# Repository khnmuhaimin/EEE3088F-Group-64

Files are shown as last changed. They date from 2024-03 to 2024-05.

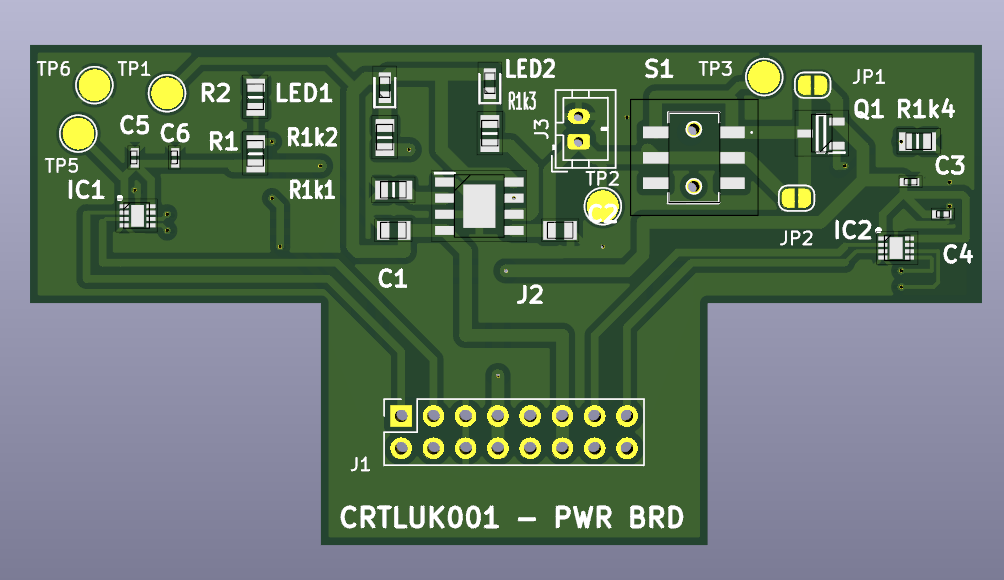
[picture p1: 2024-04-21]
power/Project Files V3/ProjectFiles/FrontPCB.png

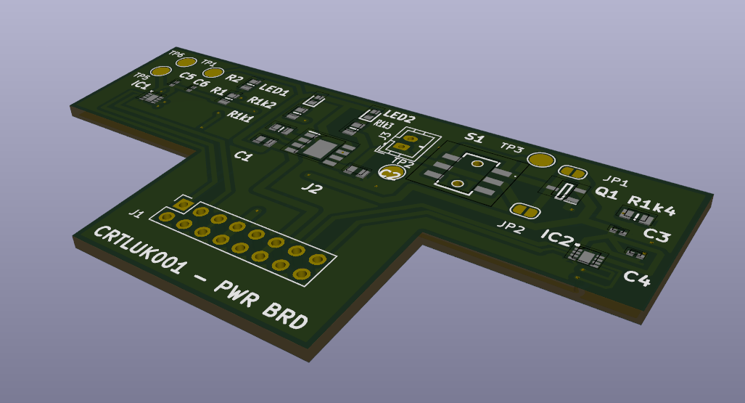
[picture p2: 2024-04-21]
power/Project Files V3/ProjectFiles/3DPCB.png

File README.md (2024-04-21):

# EEE3088F Micromouse Design Project

## Overview

This repository contains the design and implementation of the sensing and power subsystems for a micromouse project. The sensing subsystem is responsible for detecting walls and approximating distances to these walls using infrared (IR) sensors. The power subsystem is responsible for supplying power to the rest of the micromouse and controlling the motors used to move the micromouse around. This README provides an overview of the project.

## General Micromouse Features

- **Wall Detection**: Detects the presence of walls in three directions: forwards, left, and right.
- **PCB Design**: Includes the design of a custom PCB that integrates with the micromouse.
- **Autonomous Navigation**: Explores and solves a maze autonomously.

## Necessary Additional Components
- **STM32L476 microcontroller**
- **Motherboard PCB with PIN connections**
- **Wheels and motors for movement (multi-rotational drawing approximately 200mA each**
- **Battery LiPo 800mAh 3.7V**
- **Battery, Power and Sensing headers need to be purchased and soldered on during assembly**
- **5V Power supply for charging**
- **Device capable of running MATLAB**

## Installation

1. Clone the repository:

    ```
    git clone https://github.com/khnmuhaimin/EEE3088F-Group-64.git
    ```

2. Navigate to the project directory:

    ```
    cd EEE3088F-Group-64
    ```

3. Use KiCad to open up the project files for the custom PCB design.

## License

This project is licensed under the MIT License. See the `LICENSE` file for details.

## Contributors (Group 64)

- Luke Carter(CRTLUK001)
- Muhaimin Khan(KHNMUH063)

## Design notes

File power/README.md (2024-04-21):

# Power section 
Relevant files related to the power section relating to the PCB files, schematics and images from the finished product

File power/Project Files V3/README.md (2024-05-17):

# Project Files
Power project files v3 which are the final files for the project

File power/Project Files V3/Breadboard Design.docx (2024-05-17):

Breadboard Design:

Basic requirements:

- 1.5A output current
- 12V output voltage
- 2.4V transition on
- 0.5V transition off
- Current draw no more than 1mA on input stage
- Circuit operates at 12V
- Voltage across load is at least 11.5V at 1.5A
- Switching speed ON-OFF/OFF-ON less than 1us

Possible Transistors that reach the above requirements:

2N2222 – not enough current can go through

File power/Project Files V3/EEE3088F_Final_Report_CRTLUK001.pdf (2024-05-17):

# Final Design Report

Micro-mouse Power Subsystem


Prepared by:
Luke Carter

Prepared for:
EEE3088F
Department of Electrical Engineering University of Cape Town

May 17, 2024

# Declaration

1. I know that plagiarism is wrong. Plagiarism is to use another’s work and pretend that it is one’s own.
2. I have used the IEEE convention for citation and referencing. Each contribution to, and quotation in, this report from the work(s) of other people has been attributed, and has been cited and referenced.
3. This report is my own work.
4. I have not allowed, and will not allow, anyone to copy my work with the intention of passing it off as their own work or part thereof.

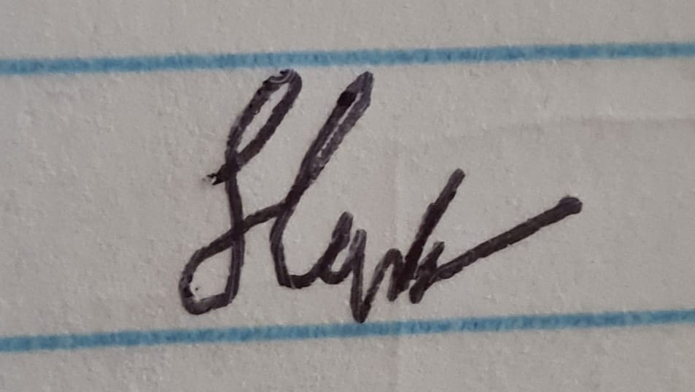
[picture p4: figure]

May 17, 2024

Name Surname | Date

ii

# Contents

1 Introduction | 1
2 Requirements Analysis | 2
3 Subsystem Design | 6
4 Acceptance Testing | 11
5 Conclusion | 18
Bibliography | 19

iii

# Chapter 1

# Introduction

### 1.1 Problem Description

This project aims at investigating and implementing a viable power system as a subsection to a micro-mouse system, capable of powering all necessary components of the system by utilizing a battery. The power subsection is part of a greater system under which two people are working towards creating a micro-mouse [1]. The micro-mouse is being created to complete a maze in the shortest time possible, where the mouse will first go through an entire maze recording the dimensions and paths of the maze, before calculating the fastest route through the maze and completing that journey, all within a 20-minute time limit, through the use of algorithms utilizing the physical components the students are designing. The other student will be working on the sensing subsystem, which will be used for the micro-mouse to detect walls for coordinated movement through the maze. Alongside these two subsystems, a processor and motherboard have been provided for integration purposes between the two subsystems allowing for control of the micro-mouse’s movement at a later stage of development.

This report focuses on the development of the power subsystem to ensure power is given to the other subsystems and to the motors, which will be needed for the movement of the micro-mouse, and to be able to communicate important information to and from the processor to allow for coordinated movement and battery charge control.

### 1.2 Scope and Limitations

This project has a specific focus on the power subsection of the micro-mouse, with the focus for this subsection establishing a working power system capable of charging batteries needed to power the system once it is unplugged from the 5V power storage and then using the charged batteries to power the micro-controller, motors and other parts of the board. Although the sensing subsection will ultimately utilize power from the power system, it is not within the scope to provide the other subsection with a specific power as they will receive the power straight from the micro-controller itself.

Limitations in the project include budget, dimensions of the PCB, specifications of parts provided to the students and components available at JLCPCB, which all need to be considered when designing the board. Full freedom outside of this is given to students with regard to choosing components and board shapes.

### 1.3 GitHub Link

https://github.com/khnmuhaimin/EEE3088F-Group-64.git

# Chapter 2

# Requirements Analysis

### 2.1 Requirements

The requirements for a micro-mouse power module are described in Table 2.1.

Table 2.1: Requirements of the power subsystem for the micro-mouse system.

Requirement ID | Description
R01 | Use a battery as the method of power for the subsystem
R02 | Operate two motors from available pins
R03 | Provide an analogue connection to verify the battery state of charge
R04 | Battery charged from the 5V pin
R05 | The system needs an on/off switch for the battery
R06 | The connector for the PCB needs to be in a tab off the board for a proper connection with the motherboard
R07 | Make PCB as small as possible to minimize the distance from the centre of rotation
R08 | Provide power to all subsections of the micro-mouse and components linked to the power sub-section e.g. the motors.

### 2.2 Specifications

The specifications, refined from the requirements in ??, for the micro-mouse power module are described in Table 2.2.

Table 2.2: Specifications of the power subsystem derived from the requirements in Table 2.1.

Specification ID | Description
SP01 | Battery is able to sustain a draw of 400mA at 4.2V
SP02 | Two Motors capable of rotating clockwise and anti-clockwise, each drawing 200mA,

2.3. Testing Procedures
SPO3 | 3.3 maximum output voltage for BATT_ADC line
SPO4 | Battery charged at 4.2V
SPO5 | Switch must handle 1A in on state and less than 1mA in off state
SPO6 | Tab height must be 18mm or greater and width height of no more than 35mm
SPO7 | PCB on micro-mouse must not exceed the distance from center of rotation of 100mm
SPO8 | Motors provided with 4.2V ±5%

### 2.3 Testing Procedures

A summary of the testing procedures detailed in chapter 4 is given in Table 2.6.

Table 2.5: Acceptance Testing Proecdures

Acceptance Test ID | Description
AT01 | Verify the battery is receiving 4.2V from the battery charger
AT02 | Verify the battery charger is getting 5V input
AT03 | Verify the switch is allowing 4.2V through when in On state
AT04 | Verify the switch is not allowing voltage through when in Off state
AT05 | Verify battery charger is outputting volt-age, used to verify there is not a short be-tween the battery connector and charger
AT06 | Verify the motor 1 will spin clockwise when switch is on, Pin 14 is high and Pin 16 is low

2.4. Traceability Analysis

Table 2.6: Acceptance Testing Proecdures

Acceptance Test ID | Description
AT07 | Verify the motor 1 will spin anti-clockwise when switch is on, Pin 16 is high and Pin 14 is low
AT08 | Verify the motor 2 will spin clockwise when switch is on, Pin 2 is high and Pin 4 is low
AT09 | Verify the motor 2 will spin anti-clockwise when switch is on, Pin 4 is high and Pin 2 is low
AT10 | Verify BATT_ADC is outputting voltage when switch is on
AT11 | Verify BATT pin which will be connected to the microprocessor is outputting a volt-age of 4.2V
AT12 | Check resistors and capacitors in the cir-cuit are not shorting

### 2.4 Traceability Analysis

The show how the requirements, specifications and testing procedures all link, Table 2.7 is provided.

Table 2.7: Requirements Traceability Matrix

# | Requirements | Specifications | Acceptance Test

1 | R01 | SP01 | AT01
2 | R02 | SP02 | AT06, AT07, AT08, AT09
3 | R03 | SP03 | AT10
4 | R04 | SP04 | AT01, AT03
5 | R05 | SP05 | AT04, AT05
8 | R08 | SP05 | AT11

R06, SP06, R07, SP07 are dimensions for the board that have been provided, no acceptance testing needs to be done for this, it just needs to be incorporated in the design section of the project AT12 are general tests that do not relate to the requirements or specifications of the project and are used to verify the board is operating correctly when it arrives

### 2.4.1 Traceability Analysis 1

R01 is the requirement that the system must be powered by a battery, with SP01 as the specification that it can sustain a draw of 400mA at 4.2V, which is verified using AT01 to check if the pins are

2.4. Traceability Analysis

producing that voltage

### 2.4.2 Traceability Analysis 2

R02 is the requirement that using available pins, two motors need to be operated, with SPO2 that they can rotate in multiple directions, each with a draw of 200mA. The motors will be spun based on a signal from the microcontroller, where there are 4 different signals, two for each motor, when one is high and another is low, it will spin in a certain direction. Using AT06, AT07, AT08 and AT09 we can verify for both batteries that they will spin in the correct direction based on the input from the microcontroller.

### 2.4.3 Traceability Analysis 3

R03 is the requirement that an analogue voltage connection is needed to verify the state of charge of the battery so the system can alert you if it is running low. SP03 indicates the max voltage on that line based on what the microcontroller can take, which will be tested using AT10 to test if the voltage is not exceeding that limit.

### 2.4.4 Traceability Analysis 4

R05 requires the battery to be charged from a 5V pin, with SP04 that the battery itself needs to be charged at 4.2V, meaning a battery charger is needed to supply 4.2V to the battery from the original 5V, which is tested using AT01 and AT03 to check correct voltages.

### 2.4.5 Traceability Analysis 5

R05 requires a working switch with SP05 that can handle 1A in on-state and 1mA in off-state. To verify the switch is working correctly AT04 and AT05 is used.

### 2.4.6 Traceability Analysis 6

R08 requires all subsystems are provided 4.2V with SP08 specifying the motors also be provided 4.2V, which is tested using AT11 which is connected to the system and motors.

# Chapter 3

# Subsystem Design

### 3.1 Design Decisions

### 3.1.1 Design Process

Within our system, different areas needed to be focused upon, each with its own challenges that needed to be solved. The three main areas of this design process were the battery charger, battery and switch system, and the motors. Within each area of the design process, several challenges need to be factored into how the final PCB was to be designed: the budget for this project was incredibly tight and certain components would therefore be out of our price range so that had to be accounted for:

- Budget - The budget for this project was incredibly tight, which made it harder when select parts as too many of certain parts would exceed the budget given, therefor considerations had to be made for each area to ensure that this project stayed below that range. The budget can be seen in the figure below:

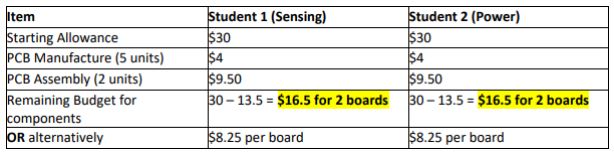
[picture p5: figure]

Figure 3.1: Budget
- Space - The PCB board had its own constraints, whereby a tab needed to be included in the design, and the dimensions of the board needed to take into consideration the turning circle of the micro-mouse such that the width and length of the PCB did not exceed the lengths. Measurements and calculations can be seen in the figure below:

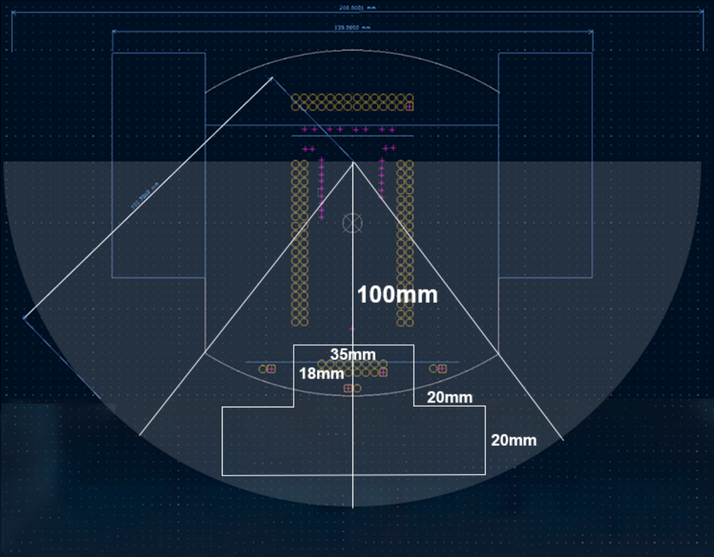
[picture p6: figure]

Figure 3.2: PCB Board Dimensions

3.1. Design Decisions
- Battery - Although the system has a good sized battery, considerations do need to be made to ensure that the components we use do not over-deplete the battery as this project needs to be able to last for over 20 minutes while navigating a maze, and using too much current will deplete the battery faster.

With the above factors in mind, each section of the sub-system can be designed accordingly to ensure that the issues mentioned above are less likely to arise.

Battery Charger

The battery charger is an integral part of the design as it will be used to charge the battery for the whole system utilizing a 5V input from the microprocessor. A voltage divider circuit could be used to reduce the voltage to the correct voltage but lacked circuit protection, and an IC charger made more sense to ensure correct protection was integrated. A primary concern with the IC battery charger was the budget aspect, as through the website the PCBs would be ordered through, JLCPCB, and certain parts would have extended costs based on whether the part was in regular production or not, resulting in the extra cost of 3 dollars for extended parts. It became apparent that the parts needed for the other sections would need to be extended, so a basic part for the charger would reduce budget concerns. This was the first major design decision, as choosing a battery charger with no extended cost greatly decreased the budget concerns, and the battery charger TP4056-42-ESOP8 became the best choice over the other options as it had no additional costs.

Switch and Battery system

Switches were a problematic area of the design as there was only one basic part switch which was a push button, which would require extra circuitry like MOSFETs, transistors, resistors and capacitors to get it to work correctly, which added complication with verifying if the circuit would work correctly, with the added specification that the switch must be added to handle 1A in the on state. This was the second major design decision made, to utilize an extended part for the switch to allow for a better selection of switches based on the type of switch and current it could handle. Based on these decisions, it was decided to use a switch called MS-22D28-G020 with verifiable data sheets and footprints for easy integration into the system, capable of handling 1A at 6V.

Motor system

The subsection required two systems each capable of running a motor at 200mA at 4.2V. Originally, the design decision was made to create an H-bridge configuration utilizing various parts such as MOSFETs and transistors to create a switching system to allow for the rotation of the motors in different directions, however, it became complicated to select the parts and to verify that the H-bridge design would function correctly with the complications of shoot-through being present in the designs. Integrated Circuits (IC) available on JLC included shoot-through protection making it a more preferable option compared to building a circuit from scratch. The third major design decision was deciding to use an H-bridge driver DRV8837DSGT, which although had an extended cost, had shoot-through protection and was designed to function according to our needs.

3.1. Design Decisions

### 3.1.2 Final Design

The following design integrates the decision decisions made above, utilizing the parts mentioned to create a system whereby a battery charger is used to charge the battery, the battery provides power to the circuit upon the switch being switched on, protected by a polarity protector. The battery will power two motors, the microprocessor and all things connected to that, and an ADC line in which the state of charge of the battery can be checked. Standard capacitors are used as a discharging method throughout, with resistors and LEDs for the TP4056 selected based on the datasheet for the component. The BATT_ADC line is protected by utilizing large resistors to protect the microprocessor.

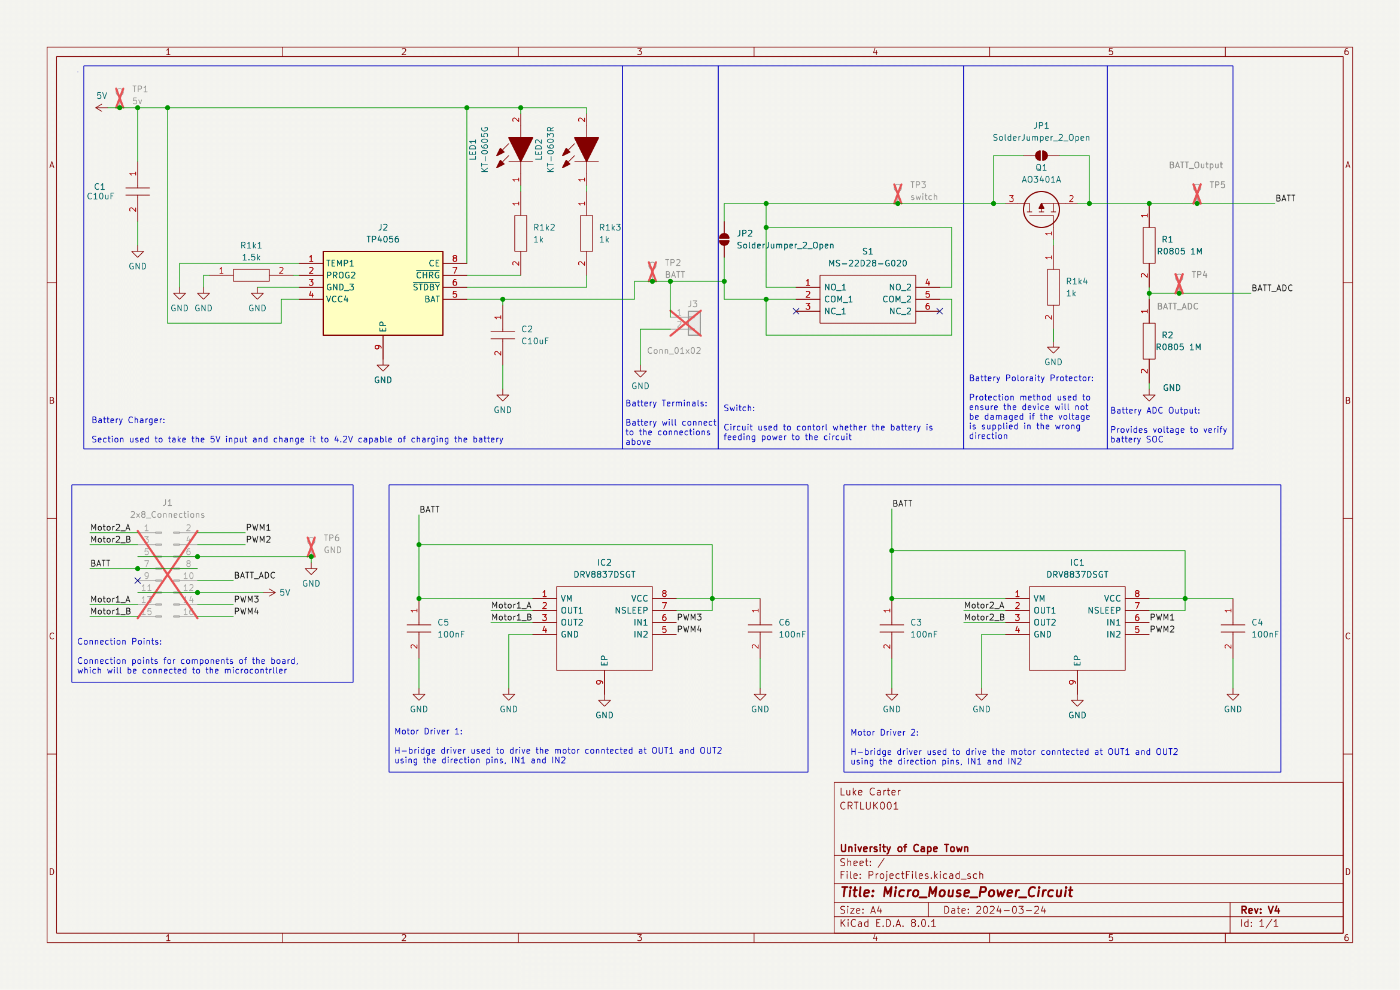
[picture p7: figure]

Figure 3.3: Schematic Drawing

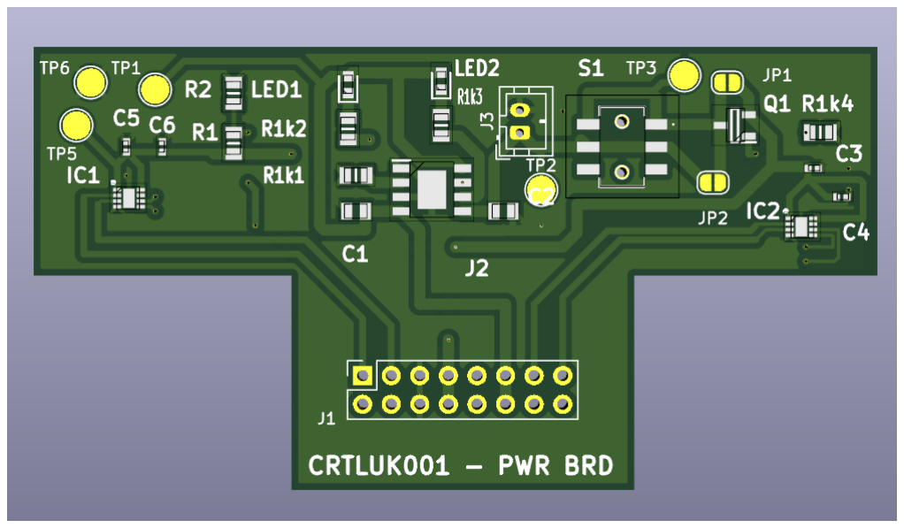
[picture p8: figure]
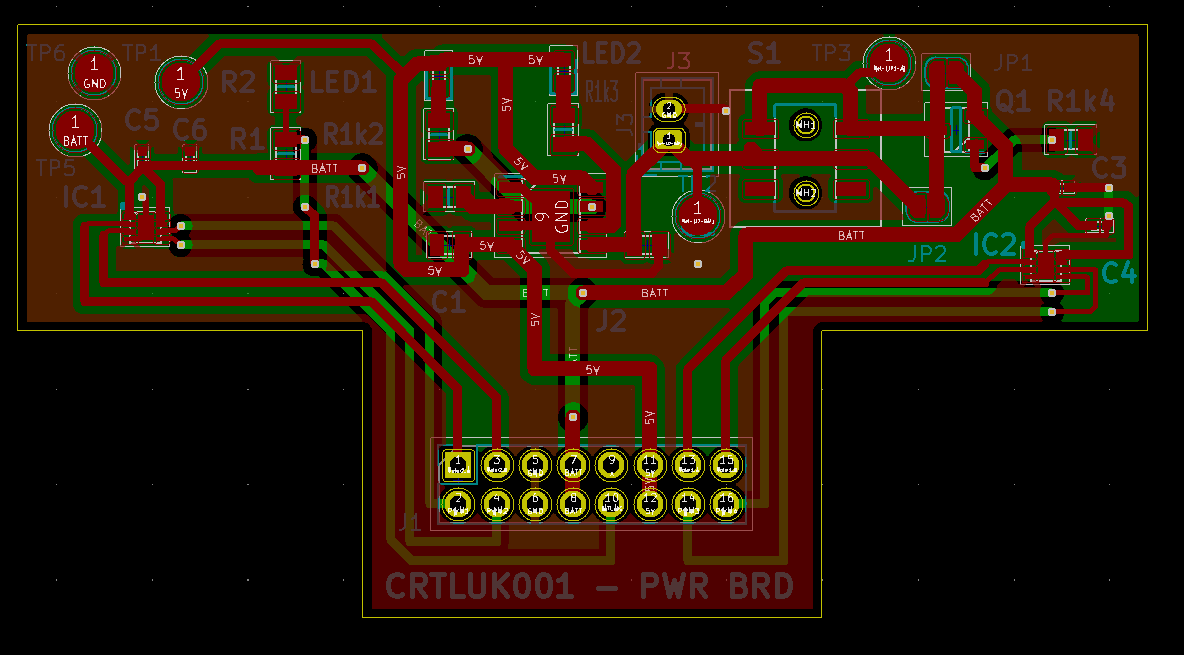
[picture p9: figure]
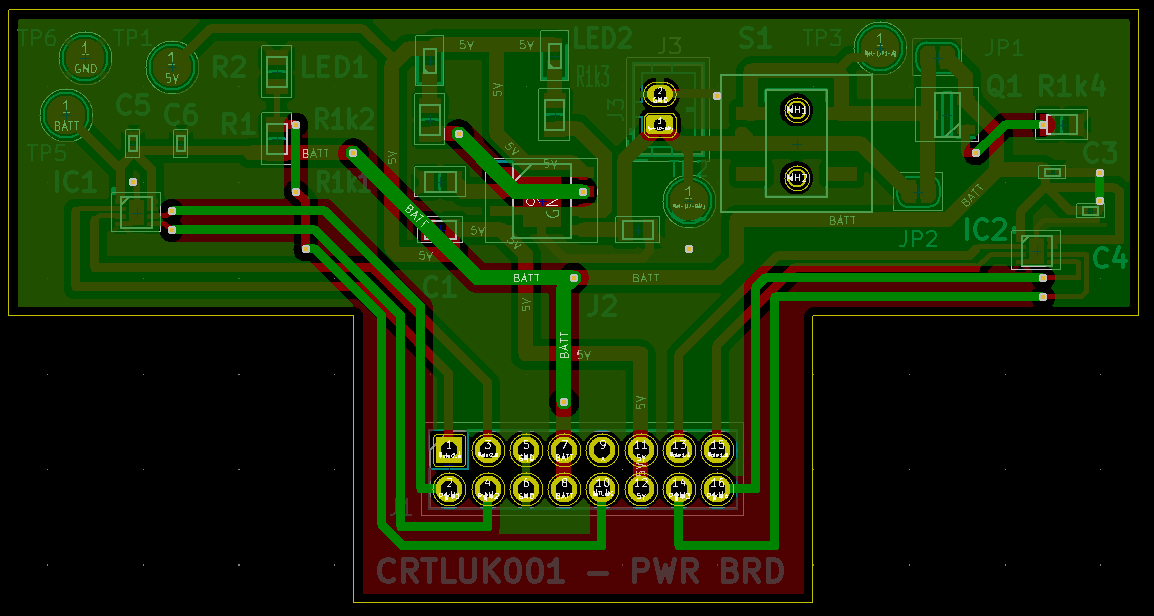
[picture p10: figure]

(a) Front PCB | (b) Back PCB | (c) 3D PCB

3.2. Failure Management

### 3.2 Failure Management

Table 3.1: Failure Management

Name | Description
Switch Bypass | The switch is an area of concern because if the switch is incorrectly selected or implemented, there could be no power coming from the battery, so a solder jumper was added over the switch such that if a problem arose, the component could be bypassed completely.
Battery Polarity Bypass | Similar to the switch, a solder jumper was added to the battery polarity protector in the case the component was dysfunctional, it could be bypassed to ensure the circuit still worked.
Testing Points at critical points | Testing points are utilized to verify certain components on the board are operating as expected by checking for shorts and measuring voltage. The testing points on the design are used before and after the battery charger, after the switch, output battery voltage and the ADC voltage pin to verify at those points in the circuit the voltage is correct or that there are no shorts.

### 3.3 System Integration and Interfacing

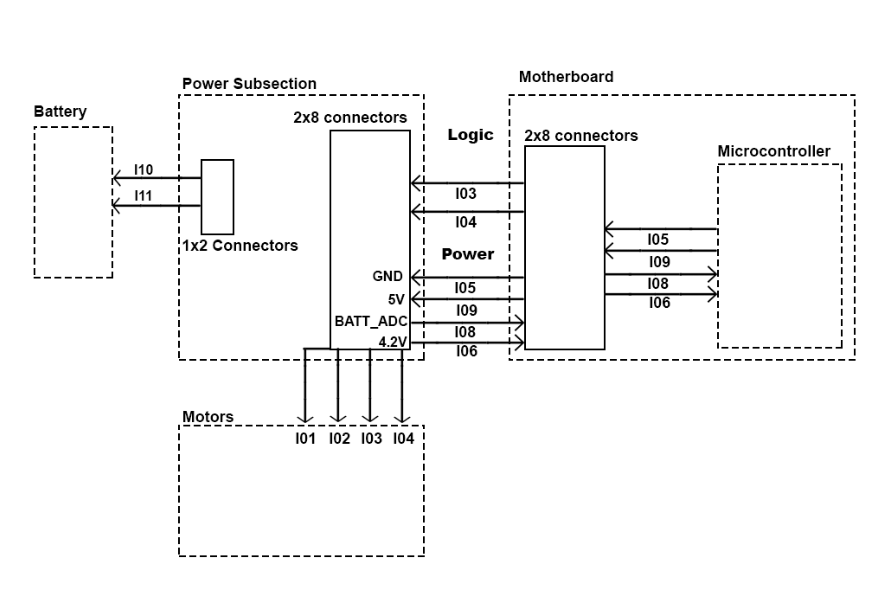
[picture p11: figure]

Figure 3.5: Interfacing Diagram

3.3. System Integration and Interfacing

Table 3.2: Interfacing specifications

Interface | Description | Pins/Output
I01 | Positive connector of motor | Pin 1, Pin 13
I02 | Negative connector of motor | Pin 3, Pin 13
I03 | Signal used to rotate motor in clockwise direction | Pin 2, Pin 14
I04 | Signal used to rotate motor in anti-clockwise direction | Pin 4, Pin 16
I05 | Ground pin to ground the power subsection using connection from microcontroller | Pin 5, Pin 6
I06 | Battery Pin used to supply a voltage of 4.2V to the microcontroller and other parts of the system | Pin 7, Pin 8
I07 | Pin which can be used for custom usage, in this case not utilized | Pin 9
I08 | Battery ADC pin used to provide the mi-crocontroller with an updated state of charge for the battery | Pin 10
I09 | 5V pin provided by the microcontroller to charge the battery | Pin 11, Pin 12
I10 | Connection to positive battery terminal | Battery Connector Pin 1
I11 | Connection to negative battery terminal | Battery Connector Pin 2

# Chapter 4

# Acceptance Testing

### 4.1 Tests

Table 4.1: Subsystem acceptance tests

Test ID | Description | Testing Procedure | Pass/Fail Criteria
AT01 | Verify the battery is re-ceiving 4.2V from the battery charger | • Plug a multi-meter in volt-age mode across the connec-tion points, postive to positive and negative to negative | Pass - 4.2V ±0.2 V is mea-sured on multi-meter
AT02 | Verify the battery charger is getting 5V input | • Using the multi-meter in voltage mode, put the positive probe on the TP1 and negative probe on TP6 | Pass - Multi-meter reads 5V
AT03 | Verify the switch is allowing 4.2V through when in On state | • Put multi-meter in voltage mode with positive probe on TP3 and negative on TP6 • Put switch on | Pass - 4.2V ±0.2 V is mea-sured on multi-meter
AT04 | Verify the switch is not allowing voltage through when in Off state | • Put multi-meter in voltage mode with positive probe on TP3 and negative on TP6 • Put switch on | Fail - Any voltage read on multi-meter
AT05 | Verify battery charger is outputting voltage, used to verify there is not a short between the battery connector and charger | • Put multi-meter on voltage mode with positive probe on TP2 and negative on TP6 | Pass - Multi-meter shows value of 4.2V ±0.5 V

4.1. Tests

Table 4.2: Subsystem acceptance tests

Test ID | Description | Testing Procedure | Pass/Fail Criteria
AT06 | Verify the motor 1 will spin clockwise when switch is on, Pin 14 is high and Pin 16 is low | • Put Multimeter in voltage mode with positive probe on Pin 13 and negative probe on Pin 15 | Pass - 4.2V ±0.3 V is mea-sured on multi-meter
AT07 | Verify the motor 1 will spin anti-clockwise when switch is on, Pin 16 is high and Pin 14 is low | • Put Multimeter in voltage mode with positive probe on Pin 13 and negative probe on Pin 15 | Pass - -4.2V ±0.3 V is mea-sured on multi-meter
AT08 | Verify the motor 2 will spin clockwise when switch is on, Pin 2 is high and Pin 4 is low | • Put Multimeter in voltage mode with positive probe on Pin 1 and negative probe on Pin 3 | Pass - 4.2V ±0.3 V is mea-sured on multi-meter
AT09 | Verify the motor 2 will spin anti-clockwise when switch is on, Pin 4 is high and Pin 2 is low | • Put Multimeter in voltage mode with positive probe on Pin 1 and negative probe on Pin 3 | Pass - -4.2V ±0.3 V is mea-sured on multi-meter
AT10 | Verify BATT_ADC is outputting voltage when switch is on | • Put multi-meter in voltage mode with positive probe on TP4 and negative on TP6 | • Pass - Multi-meter records a value of less than 3.3V • Fail - Multi-meter has a reading of 0V or above 3.3V
AT11 | Verify BATT pin which will be connected to the microprocessor is out-putting a voltage of 4.2V | • Put multi-meter in voltage mode with positive probe on TP5 and negative on TP6 | Pass - Multi-meter value records a voltage of 4.2V ±0.3 V
AT12 | Check resistors and ca-pacitors in the circuit are not shorting | • Put multimeter in continu-ity checker mode with probes across the postive and negative ends of the resistors and capac-itors on the board to check for short circuit issues | • Pass - No noise is heard • Fail - Multi-meter starts beeping

4.2. Critical Analysis of Testing

### 4.2 Critical Analysis of Testing

Table 4.3: Subsystem acceptance test results

Test ID | Description | Result
AT01 | Battery receives 4.2V | Pass
AT02 | Battery charger receives 5V input | Pass
AT03 | Switch is allowing 4.2V to pass through it | Pass
AT04 | Switch is not allowing voltage through | Pass
AT05 | Battery charger is outputting 4.2V | Pass
AT06 | Motor 1 has the correct voltage to spin clockwise based on PWM signal | Pass
AT07 | Motor 1 has the correct voltage to spin anti-clockwise based on PWM signal | Pass
AT08 | Motor 2 has the correct voltage to spin clockwise based on PWM signal | Pass
AT09 | Motor 2 has the correct voltage to spin anti-clockwise based on PWM signal | Pass
AT10 | BATT_ADC outputting voltage be-tween 0V and 3.3V | Pass
AT11 | BATT pin is receiving 4.2V (in case AT01 fails due to short) | Pass
AT12 | Resistors/Capacitors not shorting: • R1k1 • R1K2 • R1K2 • R1K3 • R1K4 • R1 • R2 • C1 • C2 • C3 • C4 | • Pass • Pass • Pass • Pass • Pass • Pass • Pass • Pass • Pass • Pass • Pass

4.2. Critical Analysis of Testing

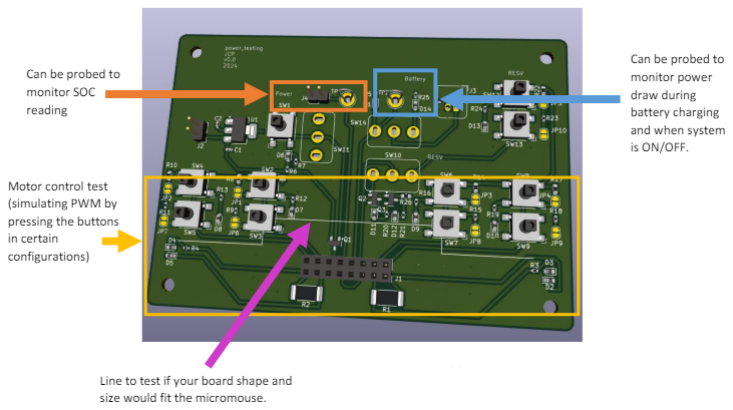
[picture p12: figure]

Figure 4.1: Testing Rig

### 4.2.1 AT01

AT01 was used to verify that the battery would be receiving 4.2V across the connector pins, from the battery charger which was provided with 5V. It was tested by powering the battery charger with 5V while the switch is off and then using a multi-meter in voltage mode with the probes connected across the 2mm pin battery connectors to verify the voltage that was being received was correct.

Testing

There were two phases of testing, the first done in a laboratory environment where the above testing procedure was followed, which resulted in a voltage ranging between 4.2V and 4.4V being recorded, which was in between the expected range, which meant it passed the acceptance test. The second phase of testing was done utilizing a testing rig seen above in the figure above, where by a battery was connected to the system to verify if the system as able to charge. When measured for a second time, a voltage of 3.9V was recorded, which although might be sufficient enough to charge the battery, was lower than expected and failed the acceptance test.

Analysis

The lower voltage recorded in the second phase of testing was 0.3V off what was expected, and after an investigation into the possible reasons why the lower voltage was recorded where the datasheet for the battery charger was investigated, it was determined that the subsequent reason that the voltage was capped at 3.9V is that when the battery becomes fully charged, the charger itself starts only outputting 3.9V to try and prevent battery overcharging which could result in long term battery efficiency issues. Once the system has utilized the power, the battery will charge at the correct voltage.

4.2. Critical Analysis of Testing

### 4.2.2 AT03

AT03 is testing whether the switch is operating correctly and will output 4.2V when the switch is in the on position. This test is done by putting a multi-meter in voltage mode from a testing point to ground to check that the voltage outputted is correct.

Testing

In the first phase of testing, the battery charger was connected to the 5V pin and the switch was turned on, and when the multi-meter was put across the testing points, the expected voltage of 4.2V was received on the other side of the switch. The second phase of testing had the same result in the on position which overall verified that the switch was working as expected when connected from the TP2 and ground on the testing rig and passed the acceptance test.

Analysis

The voltage received on the other side of the switch is 4.2V which is working as expected. However one flaw with the implementation of the switch as seen in Figure 3.3 was that the switch was implemented in what was deemed the wrong location. Although the switch operated as expected and outputted the correct voltage to the correct location, there was an issue with the actual placement of the switch as it was not placed in series with the battery terminals and instead placed after it which meant that rather than the whole circuit requiring being on when the battery charger was charging the battery, in this circuit it will only charge the battery. This might seem like a positive as none of the components will then be receiving voltage, however, there is a flaw with this as when the battery is not being used for long periods of time, it will discharge slowly over time as it is connected to ground through a capacitor after the battery charger, which means there will be an inefficiency long term, however, does not affect the overall outcome of the project, just means the battery will need to be charged before each use. This can be fixed in the design phase by moving the switch in series with the battery connectors.

### 4.2.3 AT06

AT06 is the same as AT07-AT09, just with slight modifications to what the probes are connected to and what PWM signal is provided. These acceptance tests work by measuring the voltage across the motor terminals and checking whether the voltage goes to positive 4.2V or negative 4.2V depending on what PWM signal is supplied. AT06 is checking whether Motor 1 will spin clockwise when provided with a high PWM signal in Pin 14.

Testing

In the first phase of testing, a button setup was utilized to simulate the PWM signals to Pin 14, with the multi-meter being used across the motor pins to check the voltage. Upon the button being pressed, the multi-meter read 3.99V which is within the acceptable range, and passes the acceptance test. The second phase of testing was done utilizing a testing rig, using the H-bridge setup seen in the image, where the PWM signal was given by pressing SW2 and SW5 which supplied Pin 14 with power

4.2. Critical Analysis of Testing

resulting in the voltage going high across the pins, which recorded 4.2V which is within the acceptable range and passed the acceptance test.

Analysis

Both tests showed that the motor would perform as expected, with a slight difference in the second phase of testing’s voltage reading as that system used an actual battery rather than the voltage supplied by a voltage supply from the first phase of testing which had inconsistent outputs as mentioned in AT01.

### 4.2.4 AT10

AT10 verifies if the output voltage signal is outputting a voltage that is below 3.3V to not exceed the voltage limit in the microcontroller board. It works by using a voltage divider to lower the 4.2V to a more suitable voltage to output to the system. The multi-meter is set up in voltage mode, measuring the voltage from the BATT_ADC pin to ground. Since it’s a voltage divider utilizing two resistors of equal resistance as seen in Figure 3.3, it is expected that the voltage should be around 2.1V for a fully charged battery.

Testing

During the first phase of testing, when the multi-meter was put across those terminals, it recorded a voltage of 1.3V which was lower than expected, and although it scaled as the voltage of the voltage supply changed, it did not match the expected voltage. However, since the specifications for this ADC line was a voltage of less than 3.3V, it passed the acceptance test. The second phase of testing doing the same measurement with a multi-meter resulted in the same outcome, and the acceptance test remained passed.

Analysis

The output voltage met the specified requirements and specifications, however, outputted a lower voltage than expected based on calculations, which should have been 2.1V from a fully charged battery. The suspected reason the voltage was lower than expected was that two resistors of a too-big resistance were used, which might have resulted in a bigger voltage draw than expected in the one resistor, which resulted in a lower voltage. Since it passed the acceptance test, no immediate changes need to be made, but if the PCB were to be reordered, smaller resistors should be selected to ensure better accuracy during testing.

4.2. Critical Analysis of Testing

### 4.2.5 AT12

AT12 is testing certain components in the circuit to verify they are working as intended and that there are no shorts through those components. In most of the acceptance tests, if a component is not working or shorts, it will not make a noticeable difference, other than the voltage divider for AT10, but is important for verifying all features of the circuit will perform as expected and not with slight variations. In the battery charger section, there are several capacitors used for discharging, resistors for changing the output voltage and resistors for LED protection which are needed to ensure these components do not burn out. In the polarity protector section, another resistor is used at the gate of the MOSFET to prevent oscillations in the circuit, in the voltage divider, two resistors and in the two motor sections, two discharging capacitors that all need to be verified. They can be verified by using a multi-meter in continuity mode to check if they are shorting where if the multi-meter beeps, there is a short.

Testing

For this step, there is only one phase of testing, where each component is checked to see if there is a short. Upon testing each component, it was verified that none of them shorted the PCB and they all passed the acceptance test.

Analysis

Although it might seem unnecessary to verify if all components are working as expected, through the process of testing, it was important to ensure that no components were damaged in the testing process, or that the circuit had a fault in the design, or manufacturing process that could have resulted in a fault in the circuit.

# Chapter 5

# Conclusion

### 5.1 Conclusions from the project

The purpose of this project was to develop a power subsystem capable of powering its components, two motors and a system comprising of a microcontroller, motherboard and a sensing subsystem off the use of a battery. The micro-mouse would later be utilized to traverse a maze using its built-in power system to run the system and sensing system to traverse the maze using sensors. This report investigated the implementation of a power system in order to run the micro-mouse, and through a vigorous design and testing process, the power system has met the requirements in order to sufficiently power the micro-mouse to traverse the maze for the needed duration, as the battery is able to be charged and output the correct voltage which is utilized to power the motors which when provided with PWM signals, will traverse the maze as expected. Although the switch will result in a slow discharging of the battery when not in use, the micro-mouse itself will still work as expected. Overall the project resulted in a working power system meeting the requirements needed by the user to run the power aspect of a micro-mouse while coming in under the budget requirements and fitting in the necessary dimensions that were provided.

### 5.2 Recommendations

This project has a few areas in which it can be improved, the major one being a better switch implementation where the switch is placed in series with the battery instead of after the battery and charger. Another area for improvement is smaller resistor values chosen for the battery state of charge pin for better accuracy in the expected voltage when calculations need to be done in the algorithm coding phase. One minor issue was with the PCB design itself, which did not impact the outcome of the project, was where inconsistent trace widths were used as smaller trace widths were required for the motor driver ICs and the board itself although met the dimension requirements, could be optimized to be made smaller for efficiency of space.

# Bibliography

[1] UKMARS, “Classic micromouse),” 2020. [Online]. Available: https://ukmars.org/contests/micromouse/ (https://ukmars.org/contests/micromouse/)

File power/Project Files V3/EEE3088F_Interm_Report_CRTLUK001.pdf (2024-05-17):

# Interim Design Report

Micromouse Power Subsystem


Prepared by:
Luke Carter

Prepared for:
EEE3088F
Department of Electrical Engineering University of Cape Town

April 21, 2024

# Declaration

1. I know that plagiarism is wrong. Plagiarism is to use another’s work and pretend that it is one’s own.
2. I have used the IEEE convention for citation and referencing. Each contribution to, and quotation in, this report from the work(s) of other people has been attributed, and has been cited and referenced.
3. This report is my own work.
4. I have not allowed, and will not allow, anyone to copy my work with the intention of passing it off as their own work or part thereof.


April 21, 2024

Name Surname | Date

ii

# Contents

1 Introduction | 1
2 Requirements Analysis | 2
3 Subsystem Design | 5
4 Acceptance Testing | 10
Bibliography | 12

iii

# Chapter 1

# Introduction

### 1.1 Problem Description

This project aims at investigating and implementing a viable power subsection to a micro-mouse system, capable of powering all necessary components of the system through the use of a battery. The power subsection is part of a greater system under which two people are working towards a final product where the micro-mouse, which is a miniature robot tasked with being able to move through a maze through the programming utilizing the systems we will be creating [1]. The other subsection is the sensing system, which will be used to detect walls to allow for coordinated movement of the micro-mouse. Alongside these two subsystems, a processor and motherboard have been provided for integration purposes between the two systems and will allow for the control of the micro-mouse’s movement at a later stage of development.

This report focuses on the development of the power subsystem to ensure power is given to the other subsystems and to the motors, which are needed for the movement of the micro-mouse, and to be able to communicate important information to and from the processor to allow for co-originated movement and battery charge control.

### 1.2 Scope and Limitations

This project has a specific focus on the power section, and although considerations can be made towards the sensing subsection, the majority of the focus will be establishing a working power system capable of charging batteries needed to power the system once it is unplugged and then use the charged batteries to power the micro-controller and the motors. Although the sensing subsection will utilize power from the power system, it is not within our scope to provide them with a specific power as they will be receiving the power from the micro-controller itself.

There are limitations with the actual project, although we are given full freedom on what components are utilized in the design project, we are bounded by the budget of the project, dimensions of the micro-mouse, and set specifications based on parts already chosen before use given this project such as the micro-processor and motors, all of which need to be considered during the initial design process.

### 1.3 GitHub Link

https://github.com/khnmuhaimin/EEE3088F-Group-64.git

# Chapter 2

# Requirements Analysis

### 2.1 Requirements

The requirements for a micro-mouse power module are described in Table 2.1.

Table 2.1: Requirements of the power subsystem for the micro-mouse system.

Requirement ID | Description
R01 | Use a battery as the method to power the sub-system
R02 | Operate two motors with available pins
R03 | Provide analogue connection for battery state of charge
R04 | Battery charged from 5V pin
R05 | The system needs an on/off switch
R06 | The connector for the PCB needs to be in a tab off the board for proper connection
R07 | Make PCB as small as possible to minimize the distance from the centre of rotation

### 2.2 Specifications

The specifications, refined from the requirements in Table 2.1, for the micromouse power module are described in Table 2.2.

Table 2.2: Specifications of the power subsystem derived from the requirements in Table 2.1.

Specification ID | Description
SP01 | Battery must be able to sustain a draw of 400mA at the highest voltage
SP02 | Two Motors each drawing 200mA capable of rotating clock-wise and anit-clockwise
SPO3 | Battery must be charged at 5V
SPO4 | Switch must operate when the battery is drawing less than 500uA and when the robot is operating at peak current
SPO5 | Tab height must be 18mm or greater and width height no more than 35mm
SPO6 | 3.3 ±0.5V outputvoltageforBAT T_ADCline

2.3. Testing Procedures

### 2.3 Testing Procedures

A summary of the testing procedures detailed in chapter 4 is given in Table 2.3.

Table 2.3: CAPTION

Acceptance Test ID | Description
AT01 | Verify the battery is connected correctly
AT02 | Verify the battery charge is getting 5V input
AT03 | Verify the battery is charging off 5V input
AT04 | Verify the switch is operating correctly when in on state
AT05 | Verify the switch is operating correctly when in off-state
AT06 | Verify battery charger is outputting volt-age
AT07 | Verify the motor 1 will spin clockwise
AT08 | Verify the motor 1 will spin anti-clockwise
AT09 | Verify the motor 2 will spin clockwise
AT10 | Verify the motor 2 will spin anti-clockwise
AT11 | Verify BATT_ADC is outputting voltage
AT12 | Verify BATT pin towards the microproces-sor is outputting voltage
AT13 | Check components are working

### 2.4 Traceability Analysis

The show how the requirements, specifications and testing procedures all link, Table 2.4 is provided.

Table 2.4: Requirements Traceability Matrix

# | Requirements | Specifications | Acceptance Test

1 | R01 | SP01 | AT01
2 | R04 | SP03 | AT02,AT03
3 | R02 | SP02 | AT07, AT08, AT09, AT10
4 | R05 | SP04 | AT11
5 | R03 | SP06 | AT04, AT05

### 2.4.1 Traceability Analysis 1

R01 can be derived to get SP01 as the battery is required to perform at set specifications, which we can verify using the AT01 which will test the battery is connected correctly indicating the above factors.

### 2.4.2 Traceability Analysis 2

From R04, where we charge the battery from a pin, we derive SP03 where we verify the battery is being charged at 5V, from which AT02 and AT03 tests are performed to verify that the battery is not only receiving 5V, but also charging from it.

2.4. Traceability Analysis

### 2.4.3 Traceability Analysis 3

R02 requiring functioning motors is derived to SP02 where motors draw a certain current with differing rotations, AT07-AT10 are utilized to check each of the two motors will be functioning correctly by checking there is a voltage and a rotation for the motor

### 2.4.4 Traceability Analysis 5

R05 requires an analogue signal which is derived to get SP04 which the expected voltage on that line which is checked using AT11

### 2.4.5 Traceability Analysis 4

SP06 is derived from R03 whereby the system needs a functioning on/off switch, which can be checked utilizing AT04 and AT05 tests for the different states

# Chapter 3

# Subsystem Design

### 3.1 Design Decisions

### 3.1.1 Design Process

Within our system, different areas needed to be focused upon, each with its own challenges that needed to be solved. The three main areas of this design process were the battery charger, battery and switch system, and the motors. Within each area of the design process, several challenges need to be factored into how the final PCB was to be designed: the budget for this project was incredibly tight and certain components would therefore be out of our price range so that had to be accounted for:

- Budget - The budget for this project was incredibly tight, which made it harder when select parts as too many of certain parts would exceed the budget given, therefor considerations had to be made for each area to ensure that this project stayed below that range. The budget can be seen in the figure below:
- Space - The PCB board had its own constraints, whereby a tab needed to be included in the design, and the dimensions of the board needed to take into consideration the turning circle of the micro-mouse such that the width and length of the PCB did not exceed the lengths. Measurements and calculations can be seen in the figure below:
- Battery - Although the system has a good sized battery, considerations do need to be made to ensure that the components we use do not over-deplete the battery as this project needs to be able to last for over 20 minutes while navigating a maze, and using too much current will deplete the battery faster.

With the above factors in mind, each section of the sub-system can be designed accordingly to ensure that the issues mentioned above are less likely to arise.

Battery Charger

The battery charger is an integral part of the design as it will be used to charge the battery for the whole system utilizing a 5V input from the microprocessor to charge itself for later use. A primary

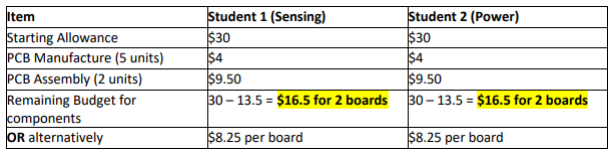
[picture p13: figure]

Figure 3.1: Budget

3.1. Design Decisions


Figure 3.2: PCB Board Dimensions

concern with the battery charger that needed to be accounted for was the budget aspect, as through the website the PCBs would be ordered through, JLCPCB, certain parts would have extended costs based on whether the part was in regular production or not, and such parts would have an extra cost of 3 dollars each. This at the time did not seem a major issue as long as multiple parts were basic instead of extended, however, it quickly became apparent that the parts needed for the other sections would also need to be extended. This was the first major design decision, whereby choosing a battery charger that had no extended cost would greatly decrease the cost of the overall budget, and the battery charger TP4056-42-ESOP8 became the best choice over the other options as although it was considered an extended part since it was previously a basic part, JLC would not add the extended part cost as with the other options.

Switch and Battery system

Switches were a problematic area of the design as there was only one switch that was a basic part, and unfortunately, it was a push button, meaning that it would be harder to implement a switch configuration from it. This was the second major design decision that was made, utilizing an extended part for the switch to allow for a better selection of switches, as in most cases it was hard to verify how the switches worked with foreign data sheets with very minimal instructional use or footprints for the PCB design. It was decided to therefore use a switch called MS-22D28-G020 which verifiable data sheets and footprints were found for easy integration into the system.

Motor system

The subsection required us to have two systems each capable of running a motor at 200mA. Originally, the design decision was made to create an H-bridge configuration utilizing various parts such as MOSFETs and transistors to create a switching system to allow for the rotation of the motors in different directions, however, it became complicated to select the parts and to verify that the H-bridge design would function correctly, and it became easier to try to find a substitute. The third major design decision was deciding to use an H-bridge extended part, which although had an increased cost, had verifiable evidence the part itself would work, and because it would be using an Integrated Circuit (IC), it would reduce the space needed for it to run, which was a major issue with the original design.

3.1. Design Decisions

### 3.1.2 Final Design

The following design integrates the decision decisions made above, utilizing the parts mentioned to create a system whereby a battery charger is used to charge the battery, the battery provides power to the circuit upon the switch being switched on, protected by a polarity protector. The battery will power two motors, the microprocessor and all things connected to that, and an ADC line in which the state of charge of the battery can be checked. Standard capacitors are used as a discharging method throughout, with resistors and LEDs for the TP4056 selected based on the datasheet for the component. The BATT_ADC line is protected by utilizing large resistors to protect the microprocessor.

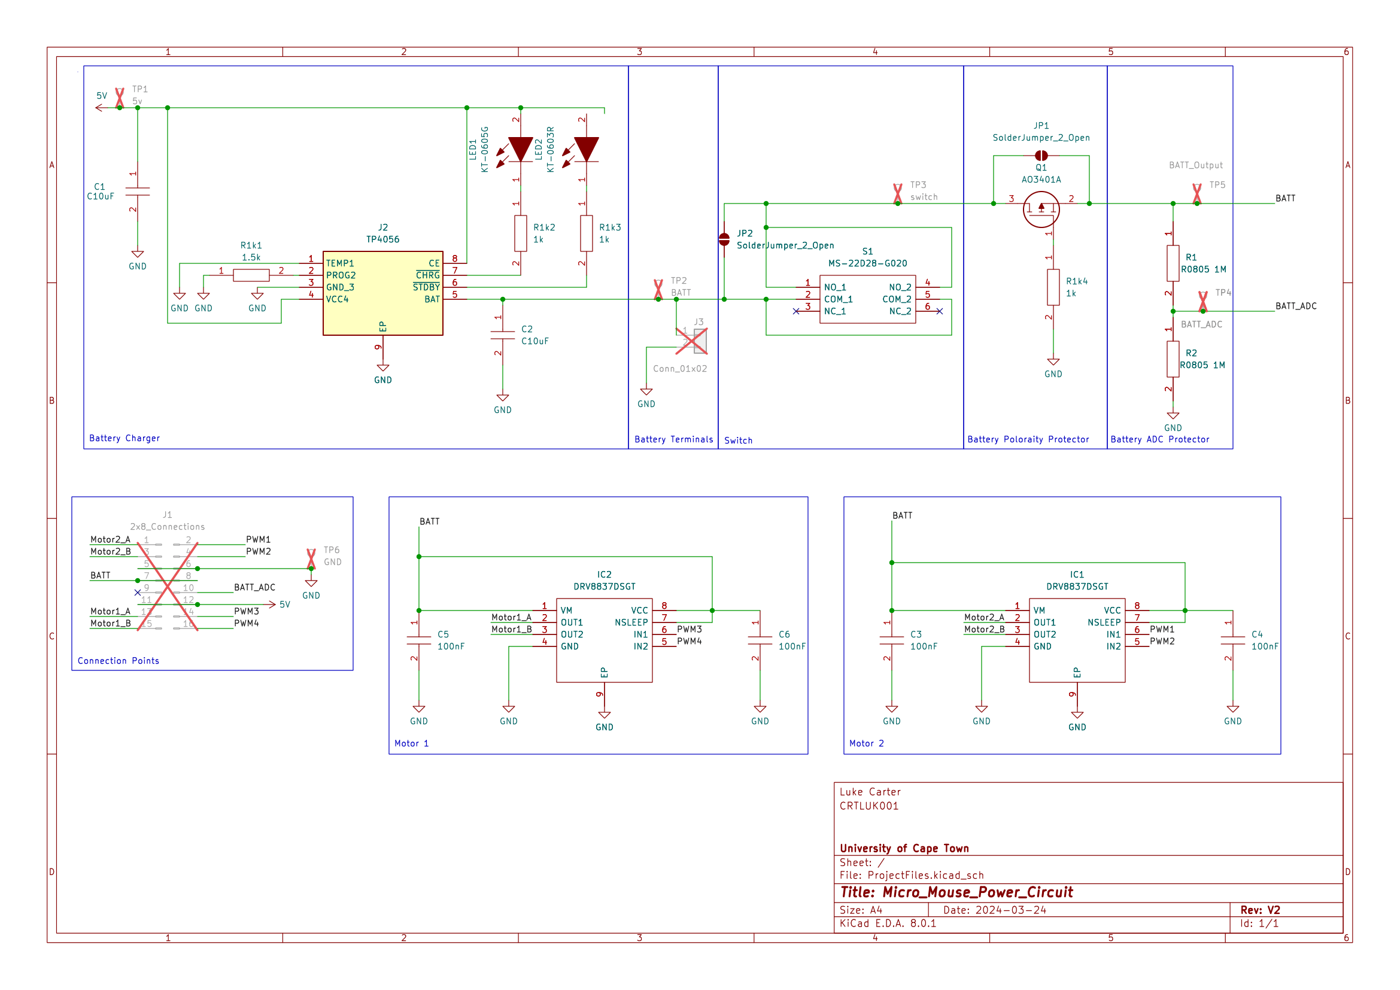
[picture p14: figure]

Figure 3.3: Schematic Drawing

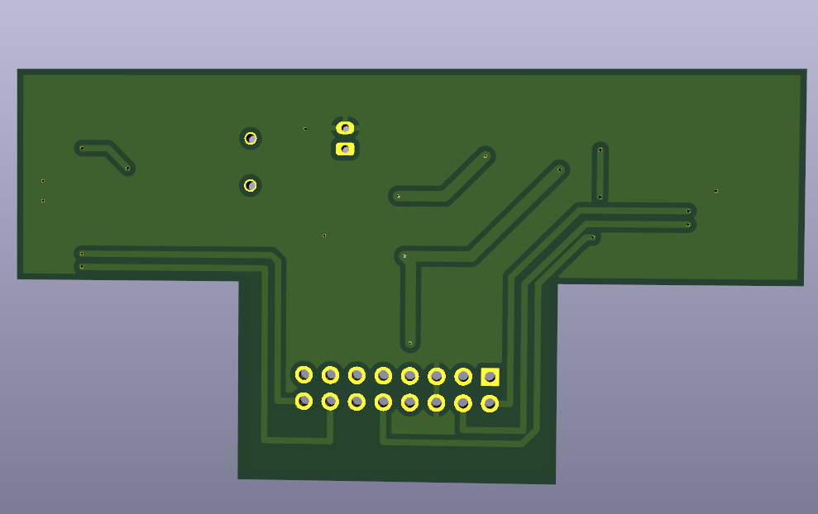
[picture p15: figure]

(a) Front PCB | (b) Back PCB | (c) 3D PCB

3.2. Failure Management

### 3.2 Failure Management

Table 3.1: Failure Management

Name | Description
Switch Bypass | The switch is an area of concern because if the switch is incorrectly selected or implemented, there could be no power coming from the battery, so a solder jumper was added over the switch such that if a problem arose, the component could be bypassed completely.
Battery Polarity Bypass | Similar to the switch, a solder jumper was added to the battery polarity protector in the case the component was dysfunctional, it could be bypassed to ensure the circuit still worked.
Motor Controller IC Placement | In the design process, the IC for the motor controller was placed on the edge of the board to prevent potential over-heating of the component as it was planned to have high current flowing through it and placing it in tight proximity to other components could increase the base temperature.
Trace Widths | Using online calculators, steps were taken to mitigate trace burning which occurs when the traces are too small, and in areas where there was high current, thicker traces were used to try to mitigate that potential problem.

### 3.3 System Integration and Interfacing

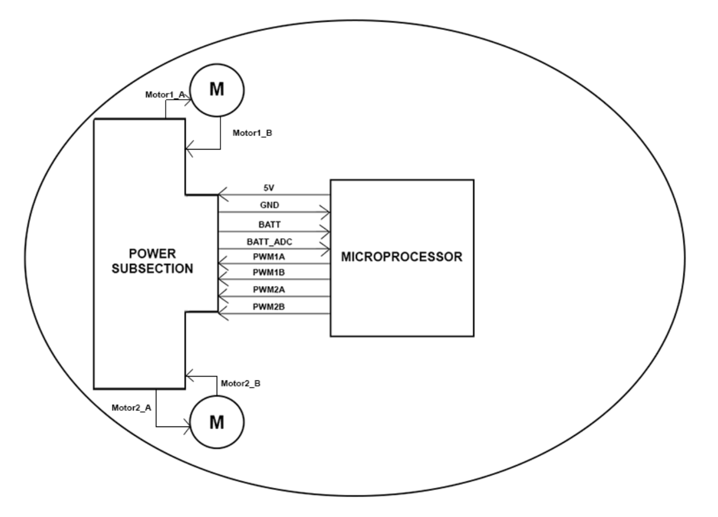
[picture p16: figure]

3.3. System Integration and Interfacing

Table 3.2: Interfacing specifications

Pins | Description | Pins/Output
1: Motor2_A | Pin from the motor controller IC on the board, to the one connection of the Motor | Motor2_A -> Motor 2 Connector Positive
2: PC6-9 | Pin from microprocessor to indicate ro-tation of motor, set clock wise or anti-clockwise | Motor2_A <- Microprocessor selected Pin
3: Motor2_B | Pin from the motor controller IC on the board, to the one connection of the Motor | Motor2_B -> Motor 2 Connector Negative
4: PC6-9 | Pin from microprocessor to indicate ro-tation of motor, set clock wise or anti-clockwise | Motor2_B <- Microprocessor selected Pin
5: GND | Ground pin used to ground the power sub-section | GND -> GND of microprocessor
6: GND | Ground pin used to ground the power sub-section | GND -> GND of microprocessor
7: BATT | Pin used to provide microprocessor with power | BATT -> Microprocessor power pin
8: BATT | Pin used to provide microprocessor with power | BATT -> Microprocessor power pin
9: PD7 | Spare pin, not in use | N/A
10: BATT_ADC | Used to check state of charge of Battery | BATT_ADC -> Microprocessor for con-version
11: 5V | 5V pin to charge the battery | 5V <- 5V supplied from the microprocessor
12: 5V | 5V pin to charge the battery | 5V <- 5V supplied from the microprocessor
13: Motor1_A | Pin from the motor controller IC on the board, to the one connection of the Motor | Motor1_A -> Motor 1 Connector Positive
14: PC6-9 | Pin from microprocessor to indicate ro-tation of motor, set clock wise or anti-clockwise | Motor1_A <- Microprocessor selected Pin
15: Motor1_B | Pin from the motor controller IC on the board, to the one connection of the Motor | Motor1_B -> Motor 1 Connector Negative
16: PC6-9 | Pin from microprocessor to indicate ro-tation of motor, set clock wise or anti-clockwiser | Motor1_B <- Microprocessor selected Pin

# Chapter 4

# Acceptance Testing

### 4.1 Tests

Table 4.1: Subsystem acceptance tests

Test ID | Description | Testing Procedure | Pass/Fail Criteria
AT01 | Verify the battery is con-nected correctly | • Plug a multi-meter across the connection points, postive to positive and negative to neg-ative | There is no voltage measured across the multi-meter mean-ing that there is no voltage travelling across the pings
AT02 | Verify the battery charge is getting 5V input | • Using the multi-meter, put the positive probe on the TP1 and negative probe on TP6 | Multi-meter shows value of 5V
AT03 | Verify the battery is charging off 5V input | • Power the system with 5V • Put the multi-meter probes across the battery | Measure the battery at two separate intervals, if the volt-age increases, the battery is being charged by the input
AT04 | Verify the switch is oper-ating correctly when in on state | • Put multi-meter positive probe on TP3 and negative on TP6 • Put switch on | Continuity checker does not make a noise
AT05 | Verify the switch is oper-ating correctly when in off-state | • Put multi-meter positive probe on TP3 and negative on TP6 • Put switch off | Continuity checker does make a noise
AT06 | Verify battery charger is outputting voltage | • Put multi-meter positive probe on TP2 and negative on TP6 | Multi-meter shows value of 4.2V±0.5V

4.1. Tests

Table 4.2: Subsystem acceptance tests

Test ID | Description | Testing Procedure | Pass/Fail Criteria
AT07 | Verify the motor 1 will spin clockwise | • Put Multimeter positive probe on Motor1_A and neg-ative probe on Motor1_B | There is a positive voltage across Motor1_A and Mo-tor1_B
AT08 | Verify the motor 1 will spin anti-clockwise | • Put Multimeter positive probe on Motor1_A and neg-ative probe on Motor1B | There is a negative voltage across Motor1_A and Mo-tor1_b
AT09 | Verify the motor 2 will spin clockwise | • Put Multimeter positive probe on Motor2_A and neg-ative probe on Motor2B | There is a negative voltage across Motor2_A and Mo-tor2_b
AT10 | Verify the motor 2 will spin anti-clockwise | • Put Multimeter positive probe on Motor2_A and neg-ative probe on Motor2_B | There is a negative voltage across Motor2_A and Mo-tor2_b
AT11 | Verify BATT_ADC is outputting voltage | • Put multi-meter positive probe on TP4 and negative on TP6 | Multi-meter records a value of 3.3V±1V
AT12 | Verify BATT pin to-wards the microproces-sor is outputting voltage | • Put multi-meter positive probe on TP5 and negative on TP6 | Multi-meter value records a voltage of 3.7V±0.5V
AT13 | Check components are working | • Put multimeter probes across the postive and negative ends of the resistors and capac-itors on the board to check for short circuit issues | Continuity checker does not go off

# Bibliography

[1] UKMARS, “Classic micromouse),” 2020. [Online]. Available: https://ukmars.org/contests/micromouse/ (https://ukmars.org/contests/micromouse/)

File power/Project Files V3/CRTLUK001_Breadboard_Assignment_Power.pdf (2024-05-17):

# Breadboard Assignment - Power


Prepared by:
Luke Carter

Prepared for:
EEE3088F
Department of Electrical Engineering University of Cape Town

March 10, 2024

# Declaration

1. I know that plagiarism is wrong. Plagiarism is to use another’s work and pretend that it is one’s own.
2. I have used the IEEE convention for citation and referencing. Each contribution to, and quotation in, this report from the work(s) of other people has been attributed, and has been cited and

referenced.

3. This report is my own work.
4. I have not allowed, and will not allow, anyone to copy my work with the intention of passing it off as their own work or part thereof.


Luke Carter | March 10, 2024
Name Surname | Date

ii

# Contents

1 Introduction | 1
2 Subsystem Design | 3
3 System Integration Design | 5
4 Conclusions | 7
Bibliography | 8

iii

# Chapter 1

# Introduction

### 1.0.1 Design problem statement

Design a circuit on a single breadboard, consisting of less than 20 components, that is able to drive a stepper motor at 1.5A and 12V using a 3V3 input logic signal running at maximum 1mA.

### 1.0.2 Context Diagram

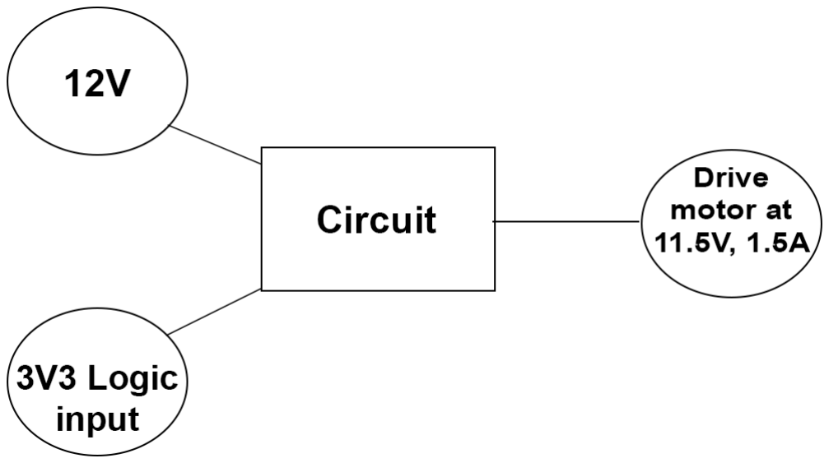
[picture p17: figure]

Figure 1.1: Context Diagram for Circuit

### 1.0.3 High-Level Requirements Diagram

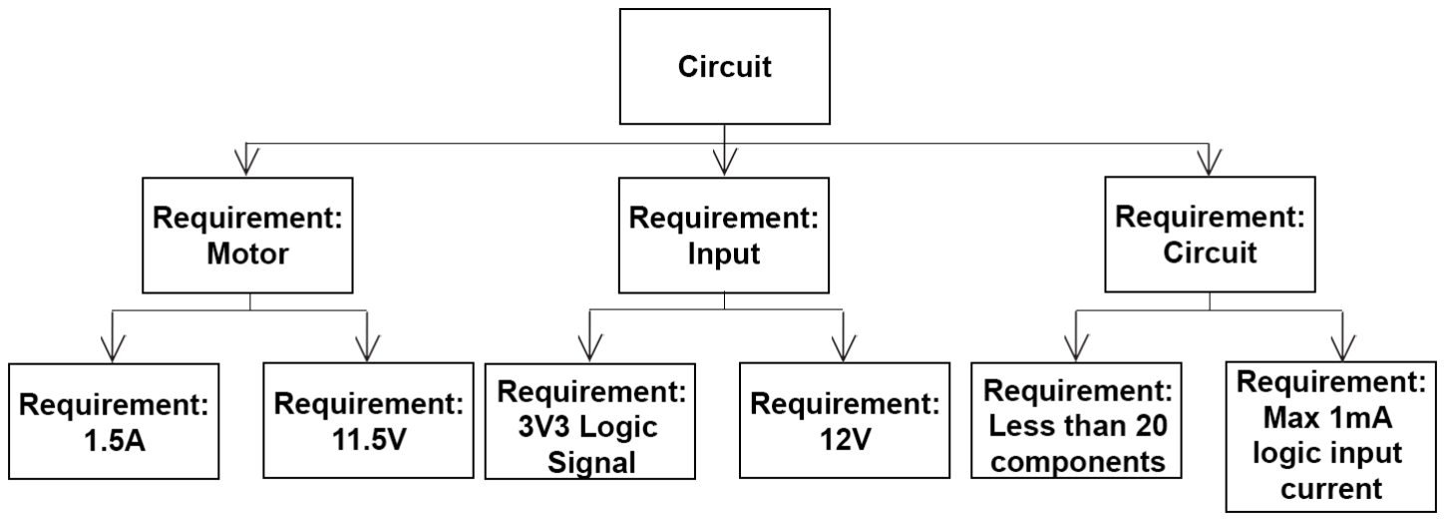
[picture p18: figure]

Figure 1.2: High-Level Requirement Diagram for circuit

### 1.0.4 Specifications and Requirements

Requirements:

- Circuit to drive a stepper motor
- Circuit must fit on a single breadboard
- Components must be sourced from White Lab
- Load on at greater than 2.4V, and off at less than 0.5V

Specifications:

- Input of 12V
- Input logic signal of 3V3
- Load must be at least 11.5V at 1.5A
- No more than 20 components
- Input logic signal must draw a maximum of 1mA
- Switching speed ON-OFF/OFF-ON at less than 1us

### 1.0.5 Discussion

The circuit needs to be able to switch on and off depending on the input logic signal being high or low, with the further requirements of it switching off at less than 0.5V and on at greater than 2.4V, which means the circuit needs to be able to check the voltage and switch the load depending the input. The best way to check for voltage input will be to use a transistor as a switching mechanism as they switch on at 0.7V or higher. 11.5V at 1.5A is extremely high so that will need to be accounted for as basic components might not be able to run at those specifications. To check the switching times, the load and the input logic signal will need to be put onto an oscilloscope which will be able to check timing differences, voltage output and current output of the circuit. Components just from white lab implies we will have a limited selection to choose from, and with the high voltage and current requirements, we will have to check data sheets to verify the components we will want to use will be able to handle the high voltage and current, and to see if they will have low enough switching speeds to handle that requirement.

# Chapter 2

# Subsystem Design

### 2.0.1 Calculations and Solution Description

Input logic signal =<1mA:

V = 3.3V, I =<1mA
R = V /I = 3.3/0.001 = 3300Ω

Using the E-series value, we can use a 3.3kΩ resistor to ensure current never exceeds 1mA.

Note:

Resistors in white lab have a 1/4th watt power rating, meaning that they cannot handle more than 1/4th of a watt, so that will need to be factored into calculations depending how high the voltage and

current is through a path

Breadboards typically cannot take more than 1A through the board without having drastic loss of voltage, so to account for this it is ideal to instead connect the points straight onto the transistors to avoid lowering the output voltage and current across the load

Although MOSFET’s were a working solution to the problem, we were not allowed to use MOSFET’s in our solution as they were not being given out in white lab. Although I had a working solution with a P MOSFET, upon reflection in the context of the assignment and the next stage, it made sense to use just basic transistors instead as the cost of a MOSFET is alot more than that of transistors and since our project is budget constrained and transistors would work just as well, it made sense to use the cheaper option that worked.

With the given information that the load was going to be connected above our circuits, it made sense to use low side switching to achieve the job. Another note, is the transistors rated enough to handle 1.5A, needed more than 1mA to power the transistor, so a pair of transistors in a darlington pair configuration was needed to successfully meet the requirements.

Since a pretty basic transistor is required to run the circuit, I selected to us a 2N2222. Although it can handle both the input of 1mA, 3V3 and 12V, the power rating on the collector side is too high as it can only handle 625 mW. With a gain of 75:

IB = 1mA

IC = β × IB = 75 × 1mA = 75mA

R = V /I = 12/0.075 = 160Ω

However, P = I

2R = 0.075² × 160 = 0.9W, which is greater than 625 mW and 0.25W that the resistors

can handle, so we need to put them in parallel and I selected to use four 680 Ω resistors

R = (1/680 + 1/680 + 1/680 + 1/680)⁻1 = 170Ω

P = I

2R = 0.01875² × 680 = 0.23W

I decided to use a TIP41C as it had the right ratings to handle the the current and voltage on collector side and could be powered from the 100mA on the base side. To demonstrate a load a 8Ω resistor can be used as it produces the right amount of current:

R = V /I = 12/1.5 = 8Ω

The circuit is powered using a constant 12V input, which is used to power the transistors and the load. The first transistor is being powered with a 3.3V input logic signal which is being used to switch the transistor and off as a way to signify the states of the motor being on and off. The first transistor is used to up the current such that the second transistor has enough current to switch on, which upon switching on is allows for the motor to run at least at 11.5V at 1.5A. The load in the schematic below is to signify the position of the motor in the circuit.

### 2.0.2 Circuit Schematic

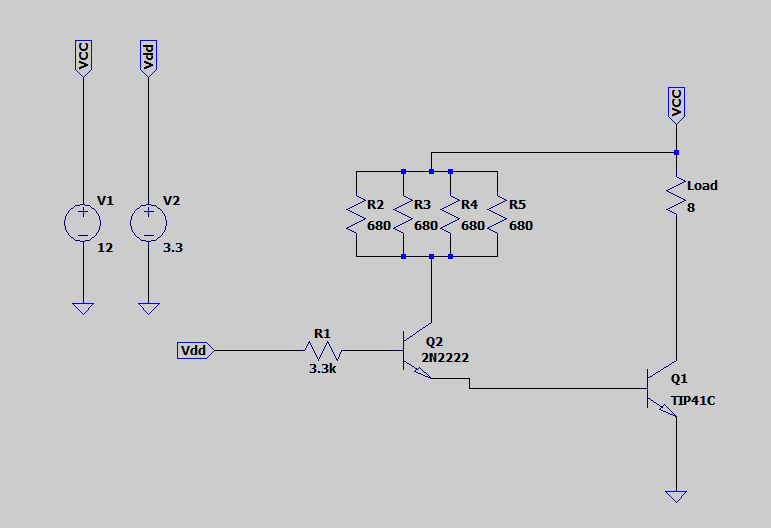
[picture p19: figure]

Figure 2.1: Circuit Schematic

# Chapter 3

# System Integration Design

### 3.0.1 Integration

The base circuit we have created can be used to power one pole of the motor in one direction. The stepper motor is a 4 pole motor and we have been given instruction we are only required to run 1 of those poles. However, this motor in the current design is only able to run in one direction as the design only has a state of on or off, neither of which can be used to change the direction of turning, which would be required for reversing the micro-mouse as given in the main project outline.

We know that the circuit is required to use low side switching, so as seen in the original schematic, we will face no problems with that, however in order for us to change the direction of the motor, we will be required to change how the motor is powered, as the motor works that based on direction of voltage flow through it will dictate the direction the motor turns, so we would need to have two different circuits powering the system such that the motor would turn based on what instruction it has been given. We haven’t been given much information relating to how the motor will be powered, but for the current design we can assume that it would essentially be two circuits similar to the ones we have made to power the motor in two different directions. With this acknowledgement, we can assess diferent methods for our integration process. One of the ideas we talked about in class was the H-bridge design.

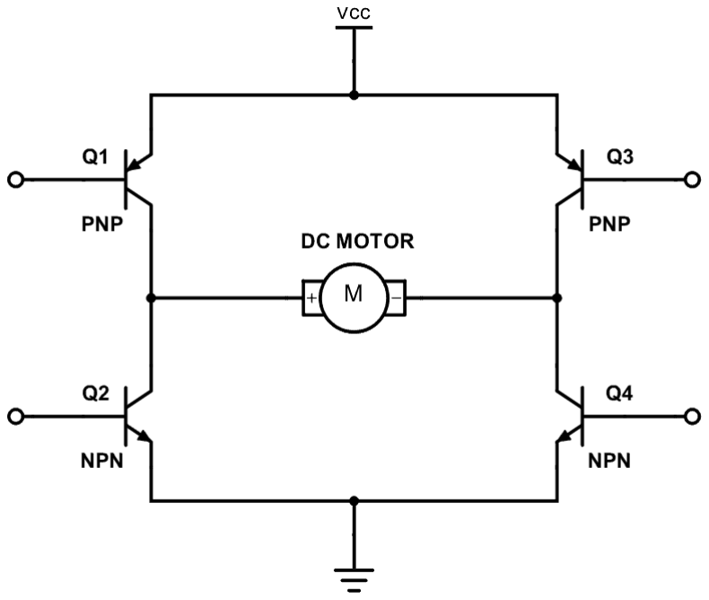
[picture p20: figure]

Figure 3.1: H-Bridge

The H-bridge design shown above works as follows, if each of the transistors above are replaced with switches, we can control the flow of voltage, so if Q1 and Q4 are closed, and Q2 and Q3 are open, the voltage will flow through the motor from left to right, and if Q1 and Q4 are open, and Q2 and Q3 are closed, it will instead flow from right to left which will allow the direction of the current to be controlled based on which switches are open.[1] These switches can be controlled using logic signals

similar to what we showed in the breadboard assignment to control the flow. Since both Q2 and Q3, and Q1 and Q4 are linked, each pair can be commanded off the same input signal so only two inputs are needed, one to signify turning clockwise, and the other turning anti-clockwise. We should be able to slot our current designs into the H-bridge without alot of major changes necessary.

### 3.0.2 System Interfacing Diagram

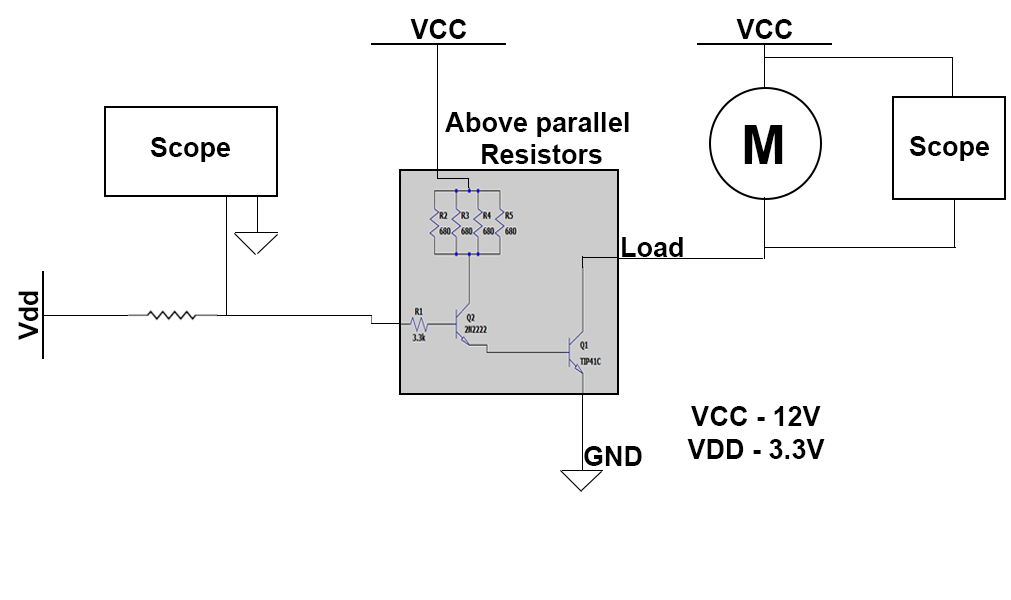
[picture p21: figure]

Figure 3.2: System Interfacing Diagram

Circuit above showcases the system we would need to connect to for testing, where the load connects and how the timing, voltages and current would be measured. The current and voltage are measured over the motor and the time for switching on and off is measured on an oscilloscope by comparing the difference between the scope and the motor’s waveform to judge how long it takes for the transistors to switch on and off.

# Chapter 4

# Conclusions

My solution met most of the requirements that were tested in the demonstration, but one area I was unable to get to work efficiently was the time for the components to switch on, although the transistors were rated at switching on and off at 1ns, this was not reflected in testing as the slowness of the switch on time led to the transition time being slower. I did try several different methods such as a bypass capacitor over the 3kΩ resistor and a bypass resistor over the TIP41C transistor, but neither seemed to achieve noticeable gains that got me close enough to the 1µs goal.

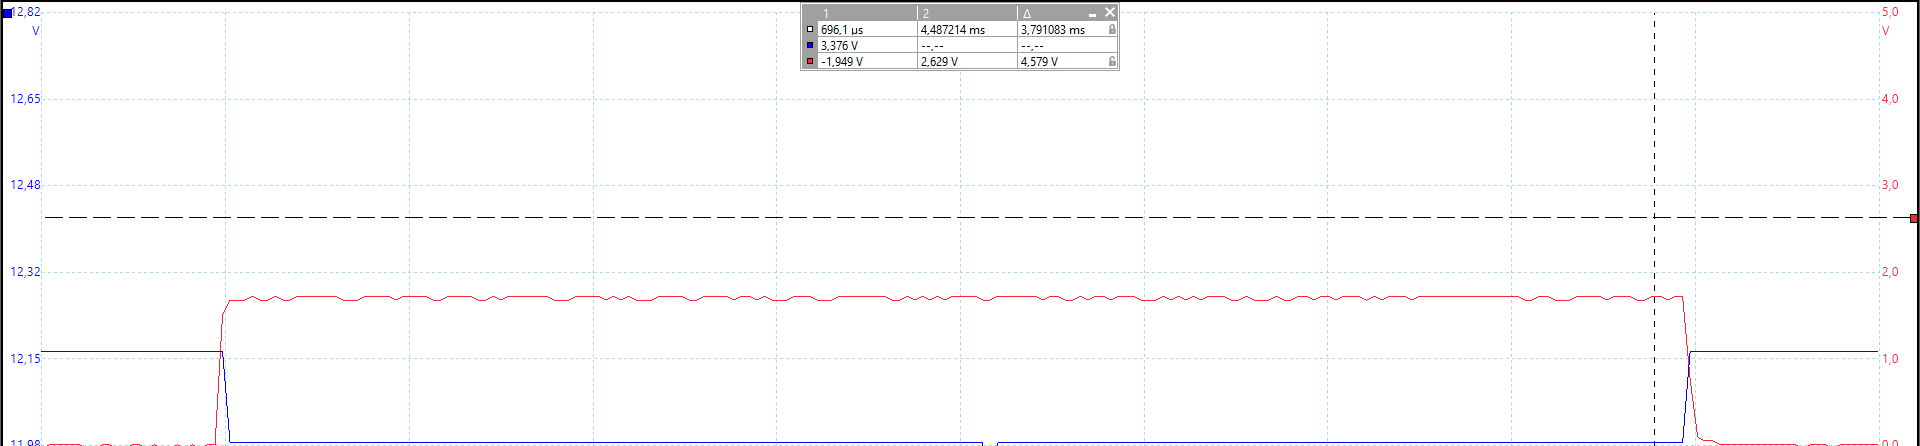
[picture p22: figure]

Figure 4.1: Oscilloscope Reference

In the image above, we can see the transitioning of the input 3.3V and 12V over the motor, which in the measurement was only able to achieve 4.4 µs in practice. It was one area which I was not able to meet the specifications set out before. Below are the requirements and specifications and how I tested them:

Requirement/Specification | Method used to test
Input of 12V Input logic signal of 3V3 No more than 20 Components 1mA on logic signal Switching speed of less than 1µs Load on at 2.4V Load off at 0.5V | Measured input voltage with a multimeter Measured logic signal using an oscilloscope Counted the components. Measured current using a multimeter Used two oscilloscope to measure input signal against motor signal Changed the input signal to 2.4V to see if it would turn on Changed the input signal to 0.5V to see if it would turn off

Table 4.1: Testing methods

# Bibliography

[1] Øyvind Nydal Dahl, | “What is an h-bridge?” | 2018. [Online]. Available: | https:
//www.build-electronic-circuits.com/h-bridge/

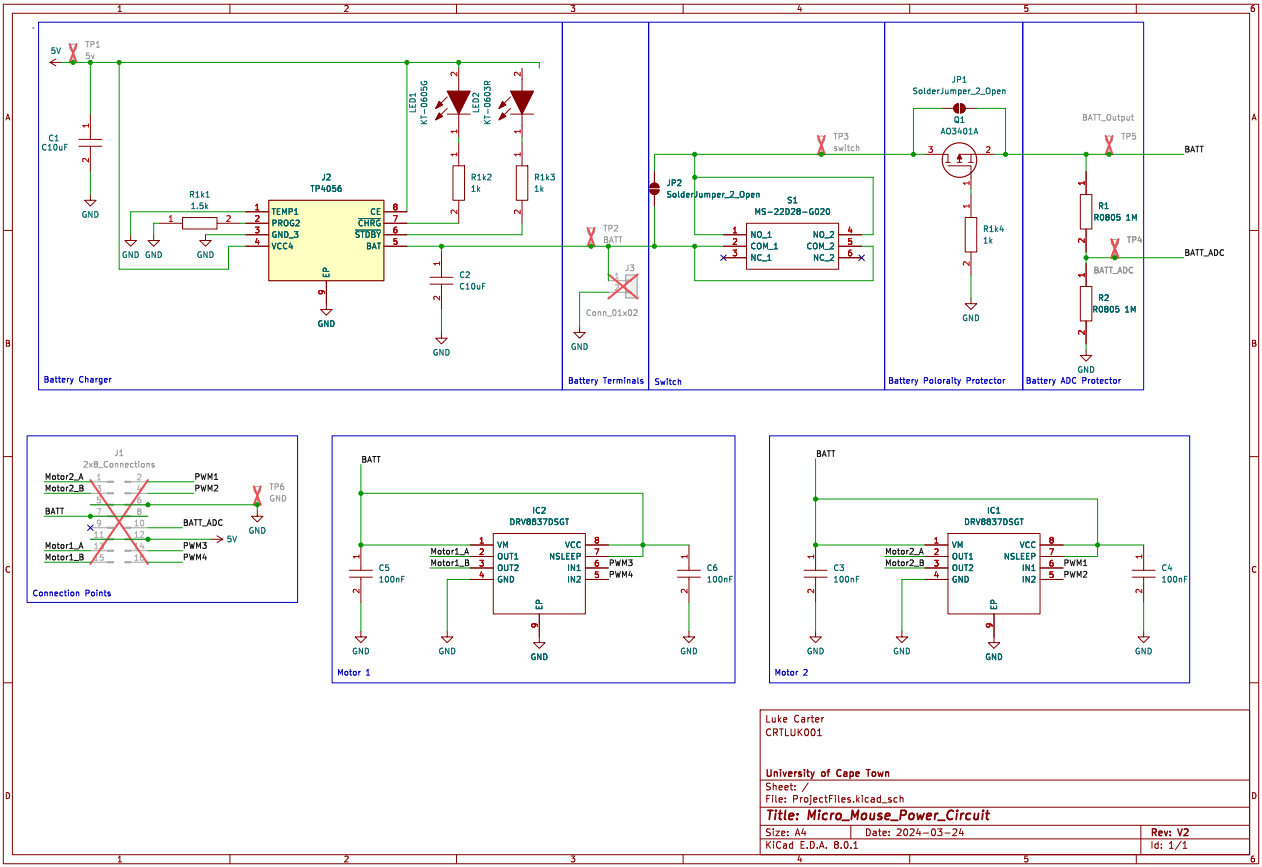
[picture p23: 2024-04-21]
power/Project Files V3/ProjectFiles/Schematic_Drawing.png

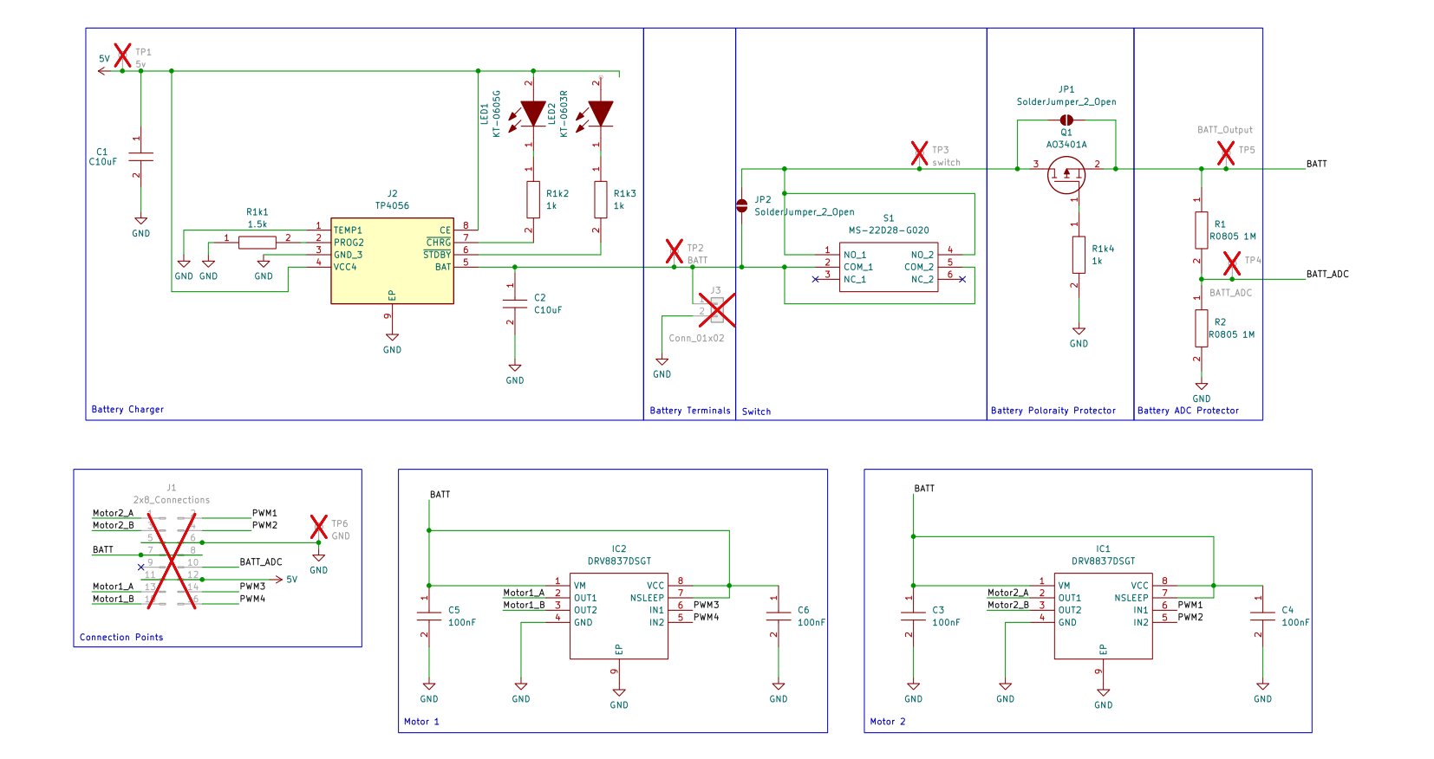
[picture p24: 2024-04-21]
power/Project Files V3/ProjectFiles/Schematic2-1.png

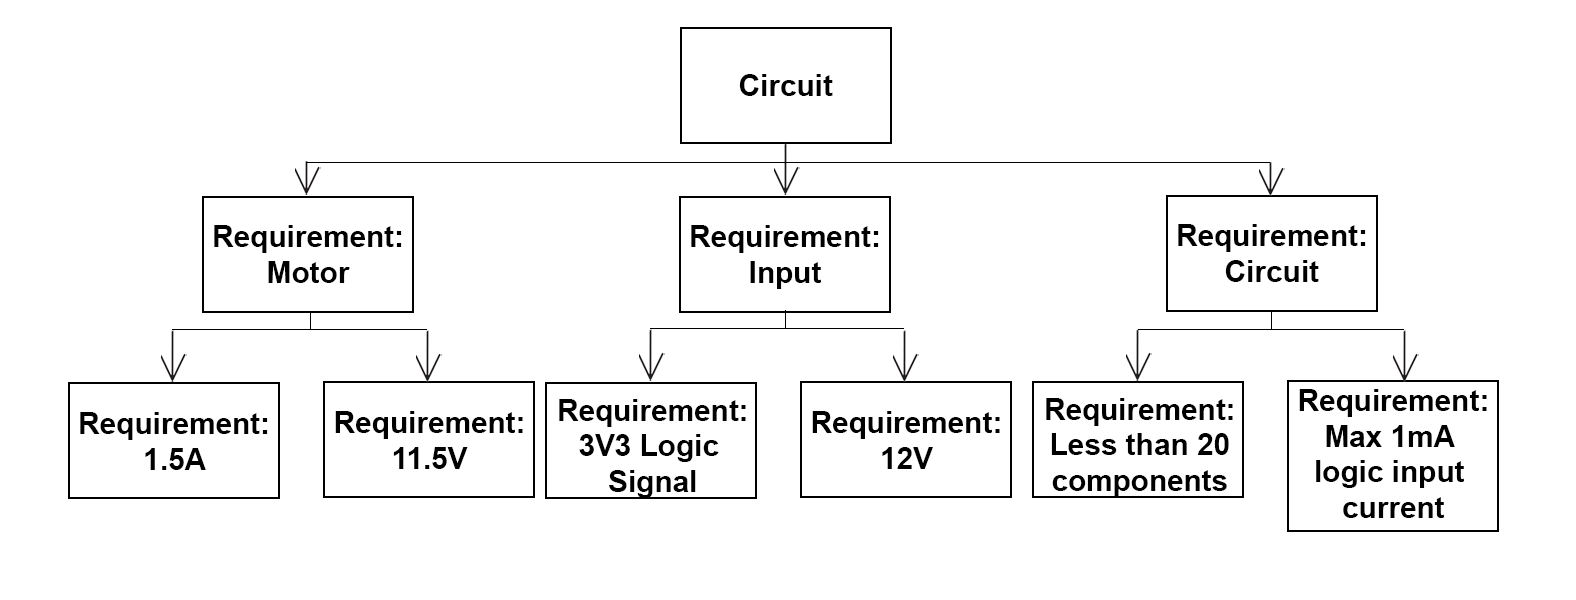
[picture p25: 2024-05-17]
power/Project Files V3/High-level_requitement_diagram.png

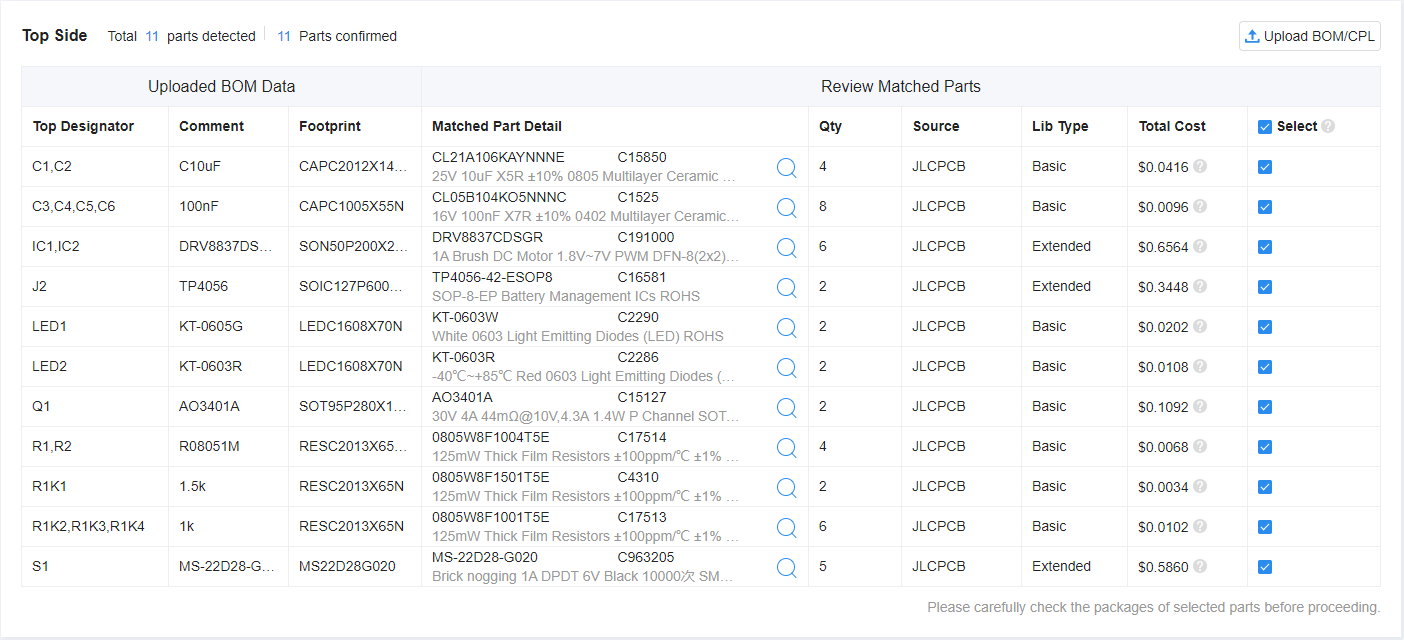
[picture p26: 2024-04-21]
power/Project Files V3/ProjectFiles/jlcpcb/production_files/EEE3088F_Project_JLCPCBBOM_CRTLUK001.png

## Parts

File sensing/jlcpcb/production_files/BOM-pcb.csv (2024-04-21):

Comment | Designator | Footprint | LCSC
BPW41N | U4,U5,U6 | SENSOR-TH_BPW41N | C142586
SFH 4544 | U1,U2,U3 | LED_D5.0mm_Horizontal_O6.35mm_Z15.0mm | C2900370
LM324DT | U7 | SOIC-14_L8.7-W3.9-P1.27-LS6.0-BL | C71035
MMBT2222A_C8512 | Q1,Q2,Q4 | SOT-23-3_L2.9-W1.3-P1.90-LS2.4-BR | C8512
1M | R1 | R_0805_2012Metric
2.2M | R7 | R_0805_2012Metric
2.2M | R9 | R_0805_2012Metric
6.8k | R6 | R_0805_2012Metric
1M | R2 | R_0805_2012Metric
6.8k | R4 | R_0805_2012Metric
6.8k | R5 | R_0805_2012Metric
1M | R3 | R_0805_2012Metric
2.2M | R8 | R_0805_2012Metric

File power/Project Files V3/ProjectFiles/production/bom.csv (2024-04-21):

Designator | Footprint | Quantity | Value | LCSC Part #
C1, C2 | CAPC2012X145N | 2 | C10uF
C3, C4, C5, C6 | CAPC1005X55N | 4 | 100nF
IC1, IC2 | SON50P200X200X80-9N | 2 | DRV8837DSGT
J2 | SOIC127P600X175-9N | 1 | TP4056
LED1 | LEDC1608X70N | 1 | KT-0605G
LED2 | LEDC1608X70N | 1 | KT-0603R
Q1 | SOT95P280X125-3N | 1 | AO3401A
R1, R2 | RESC2013X65N2 | 2 | R0805 1M
R1k1 | RESC2013X65N | 1 | 1.5k
R1k2, R1k3, R1k4 | RESC2013X65N | 3 | 1k
S1 | MS22D28G020 | 1 | MS-22D28-G020

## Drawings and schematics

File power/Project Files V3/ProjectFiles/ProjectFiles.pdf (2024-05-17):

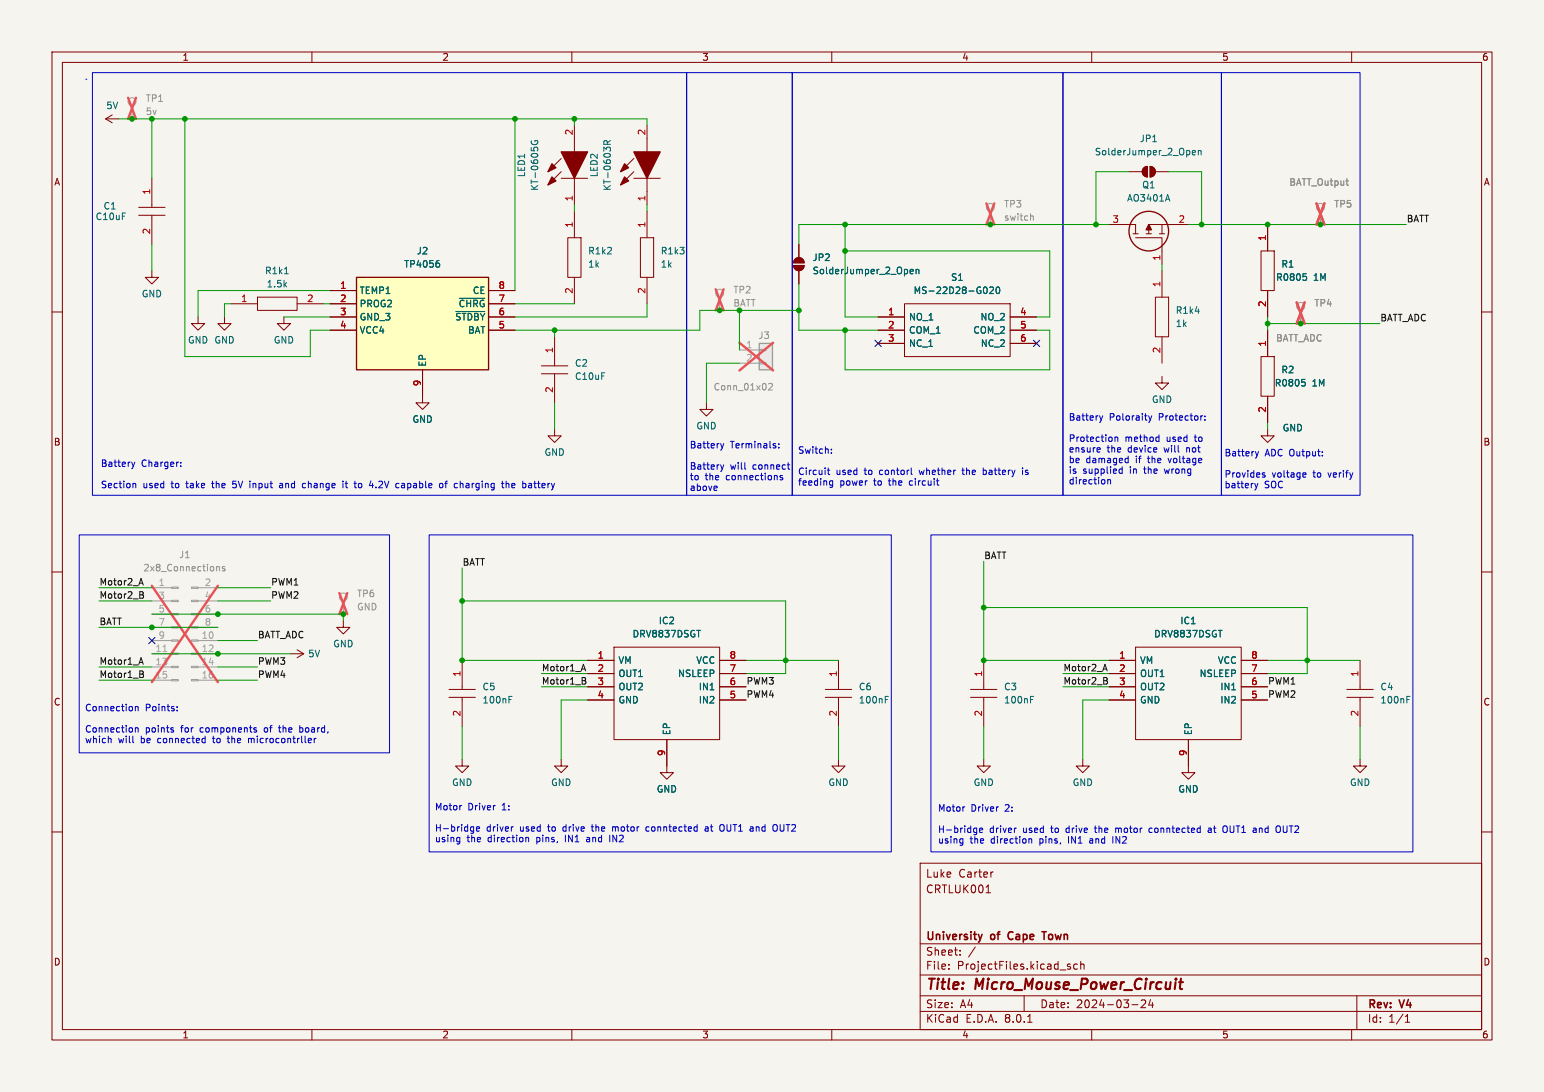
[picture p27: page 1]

Luke Carter 5V GND GND

feeding power to the circuit Battery Terminals: Battery will connect

ensure the device will not be damaged if the voltage

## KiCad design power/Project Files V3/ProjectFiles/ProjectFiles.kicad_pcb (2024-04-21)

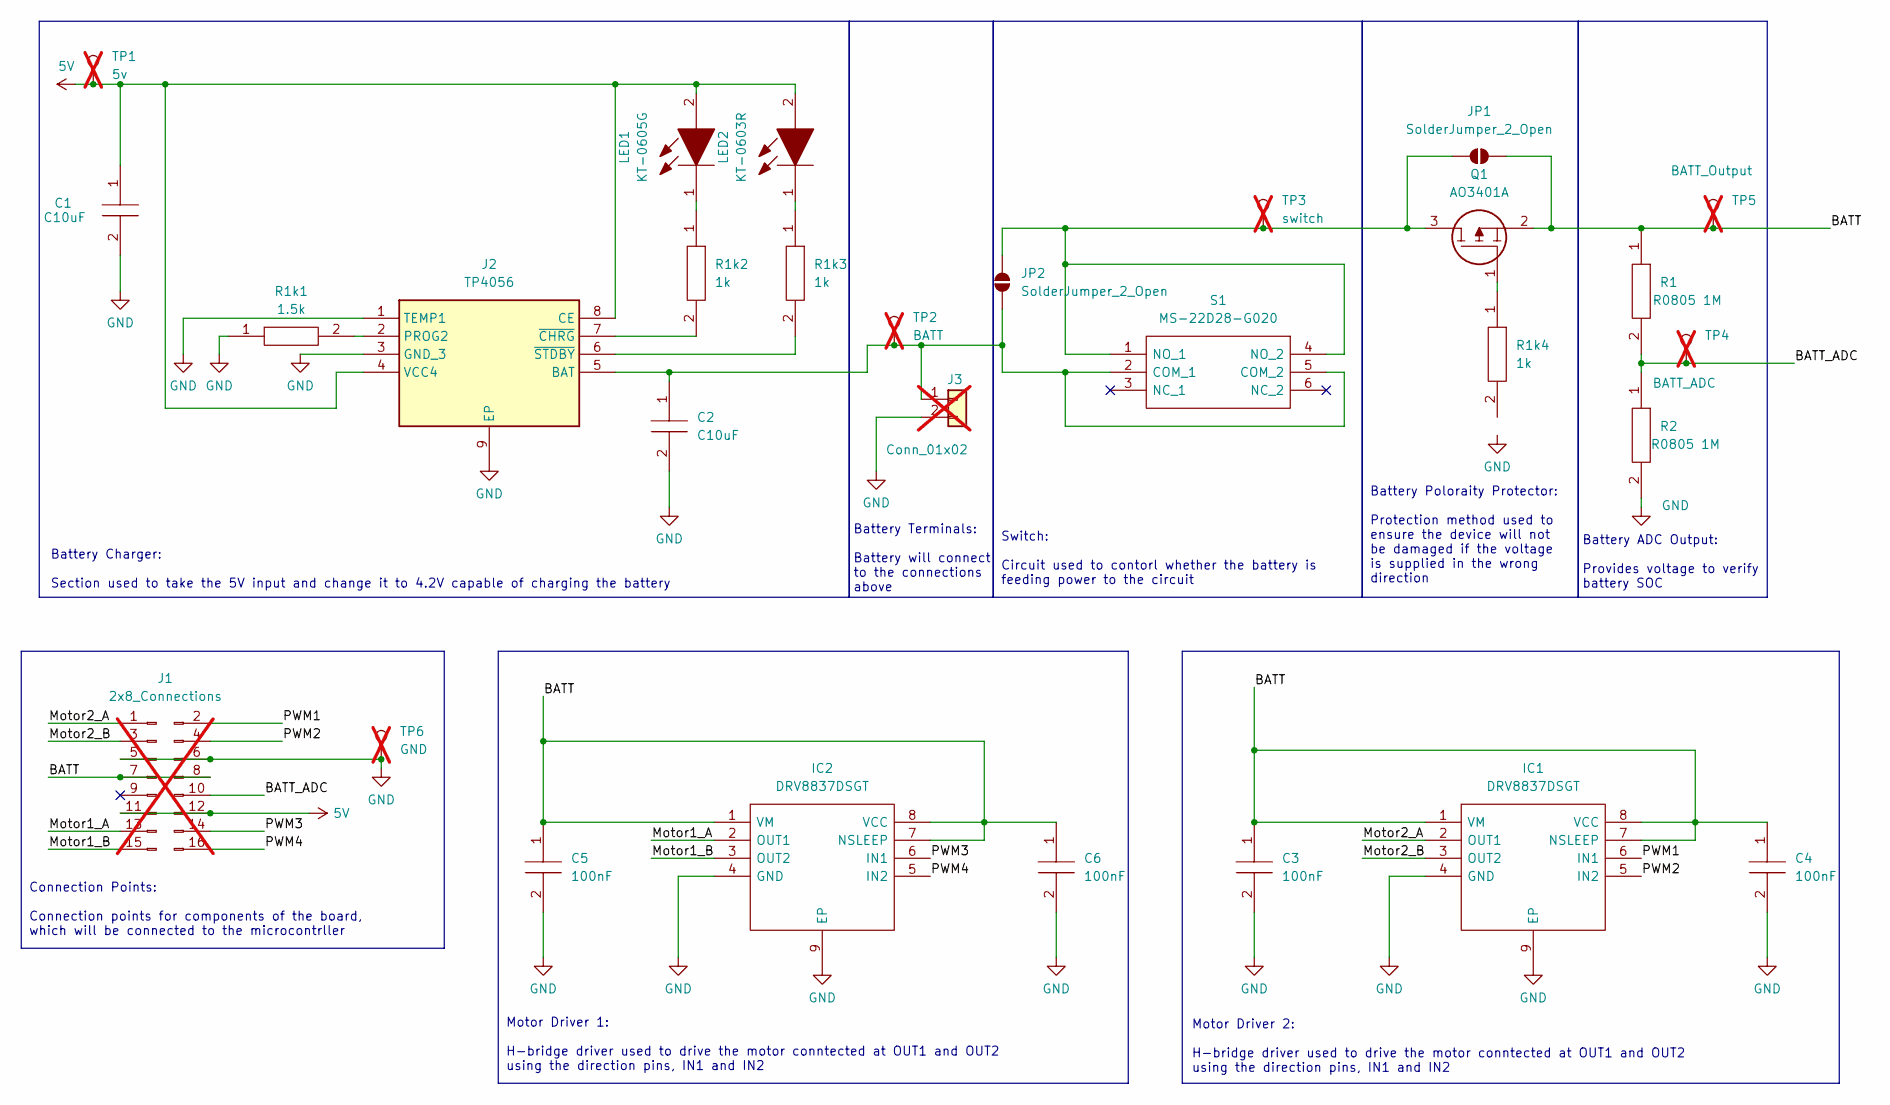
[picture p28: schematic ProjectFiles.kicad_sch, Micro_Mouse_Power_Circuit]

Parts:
C1, C2: C10uF; CAPC2012X145N
C3, C4, C5, C6: 100nF; CAPC1005X55N
IC1, IC2: DRV8837DSGT; SON50P200X200X80-9N
J1: 2x8_Connections; PinHeader_2x08_P2.54mm_Vertical; not fitted
J2: TP4056; SOIC127P600X175-9N; Manufacturer_Part_Number TP4056
J3: Conn_01x02; JST_PH_B2B-PH-K_1x02_P2.00mm_Vertical; not fitted
JP1, JP2: SolderJumper_2_Open; SolderJumper-2_P1.3mm_Open_RoundedPad1.0x1.5mm
LED1: KT-0605G; LEDC1608X70N
LED2: KT-0603R; LEDC1608X70N
Q1: AO3401A; SOT95P280X125-3N
R1, R2: R0805 1M; RESC2013X65N2
R1k1: 1.5k; RESC2013X65N
R1k2, R1k3, R1k4: 1k; RESC2013X65N
S1: MS-22D28-G020; MS22D28G020
TP1: 5v; TestPoint_Pad_D2.5mm; not fitted
TP2: BATT; TestPoint_Pad_D2.5mm; not fitted
TP3: switch; TestPoint_Pad_D2.5mm; not fitted
TP4: BATT_ADC; TestPoint_Pad_D2.5mm; not fitted
TP5: BATT_Output; TestPoint_Pad_D2.5mm; not fitted
TP6: GND; TestPoint_Pad_D2.5mm; not fitted

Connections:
5V: C1.1, J1.11, J1.12, J2.4 (VCC4), J2.8 (CE), LED1.2, LED2.2, TP1.1
/BATT: C3.1, C4.1, C5.1, C6.1, IC1.1 (VM), IC1.7 (NSLEEP), IC1.8 (VCC), IC2.1 (VM), IC2.7 (NSLEEP), IC2.8 (VCC), J1.7, J1.8, JP1.2 (B), Q1.2, R1.1, TP5.1
/BATT_ADC: J1.10, R1.2, R2.1, TP4.1
/Motor1_A: IC2.2 (OUT1), J1.13
/Motor1_B: IC2.3 (OUT2), J1.15
/Motor2_A: IC1.2 (OUT1), J1.1
/Motor2_B: IC1.3 (OUT2), J1.3
/PWM1: IC1.6 (IN1), J1.2
/PWM2: IC1.5 (IN2), J1.4
/PWM3: IC2.6 (IN1), J1.14
/PWM4: IC2.5 (IN2), J1.16
GND: C1.2, C2.2, C3.2, C4.2, C5.2, C6.2, IC1.4 (GND), IC1.9 (EP), IC2.4 (GND), IC2.9 (EP), J1.5, J1.6, J2.1 (TEMP1), J2.3 (GND_3), J2.9 (EP), J3.2, R1k1.1, R1k4.2, R2.2, TP6.1
unnamed: C2.1, J2.5 (BAT), J3.1, JP2.2 (B), S1.2 (COM_1), S1.5 (COM_2), TP2.1
unnamed: J2.2 (PROG2), R1k1.2
unnamed: J2.7 (~CHRG), R1k2.2
unnamed: J2.6 (~STDBY), R1k3.2
unnamed: JP1.1 (A), JP2.1 (A), Q1.3, S1.1 (NO_1), S1.4 (NO_2), TP3.1
unnamed: LED1.1, R1k2.1
unnamed: LED2.1, R1k3.1
unnamed: Q1.1, R1k4.1

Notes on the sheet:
Battery Terminals: Battery will connect to the connections above
Motor Driver 1: H-bridge driver used to drive the motor conntected at OUT1 and OUT2 using the direction pins, IN1 and IN2
Motor Driver 2: H-bridge driver used to drive the motor conntected at OUT1 and OUT2 using the direction pins, IN1 and IN2
Battery Charger: Section used to take the 5V input and change it to 4.2V capable of charging the battery
Connection Points: Connection points for components of the board, which will be connected to the microcontrller
Battery ADC Output: Provides voltage to verify battery SOC
Battery Poloraity Protector: Protection method used to ensure the device will not be damaged if the voltage is supplied in the wrong direction
Switch: Circuit used to contorl whether the battery is feeding power to the circuit

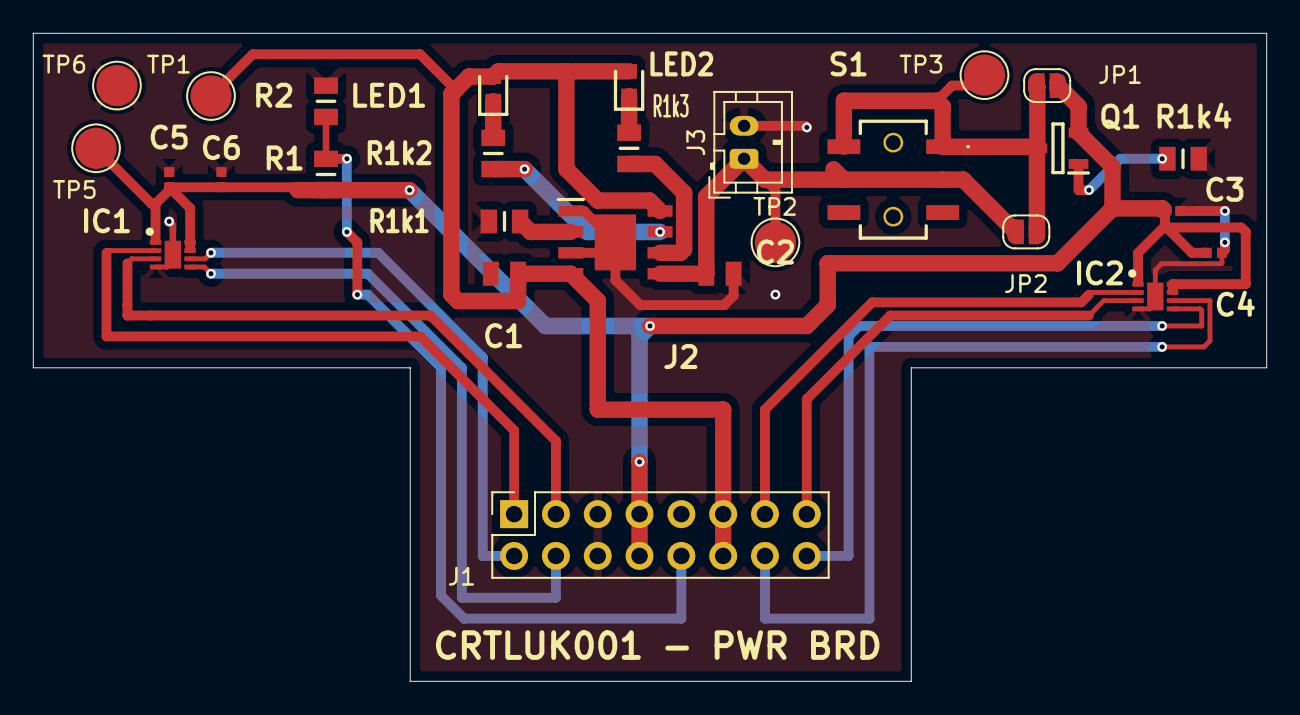
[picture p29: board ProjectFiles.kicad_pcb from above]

Board: 2 copper layers, 74.9 x 39.4 mm, 28 parts (0 on the bottom side), 20 nets.

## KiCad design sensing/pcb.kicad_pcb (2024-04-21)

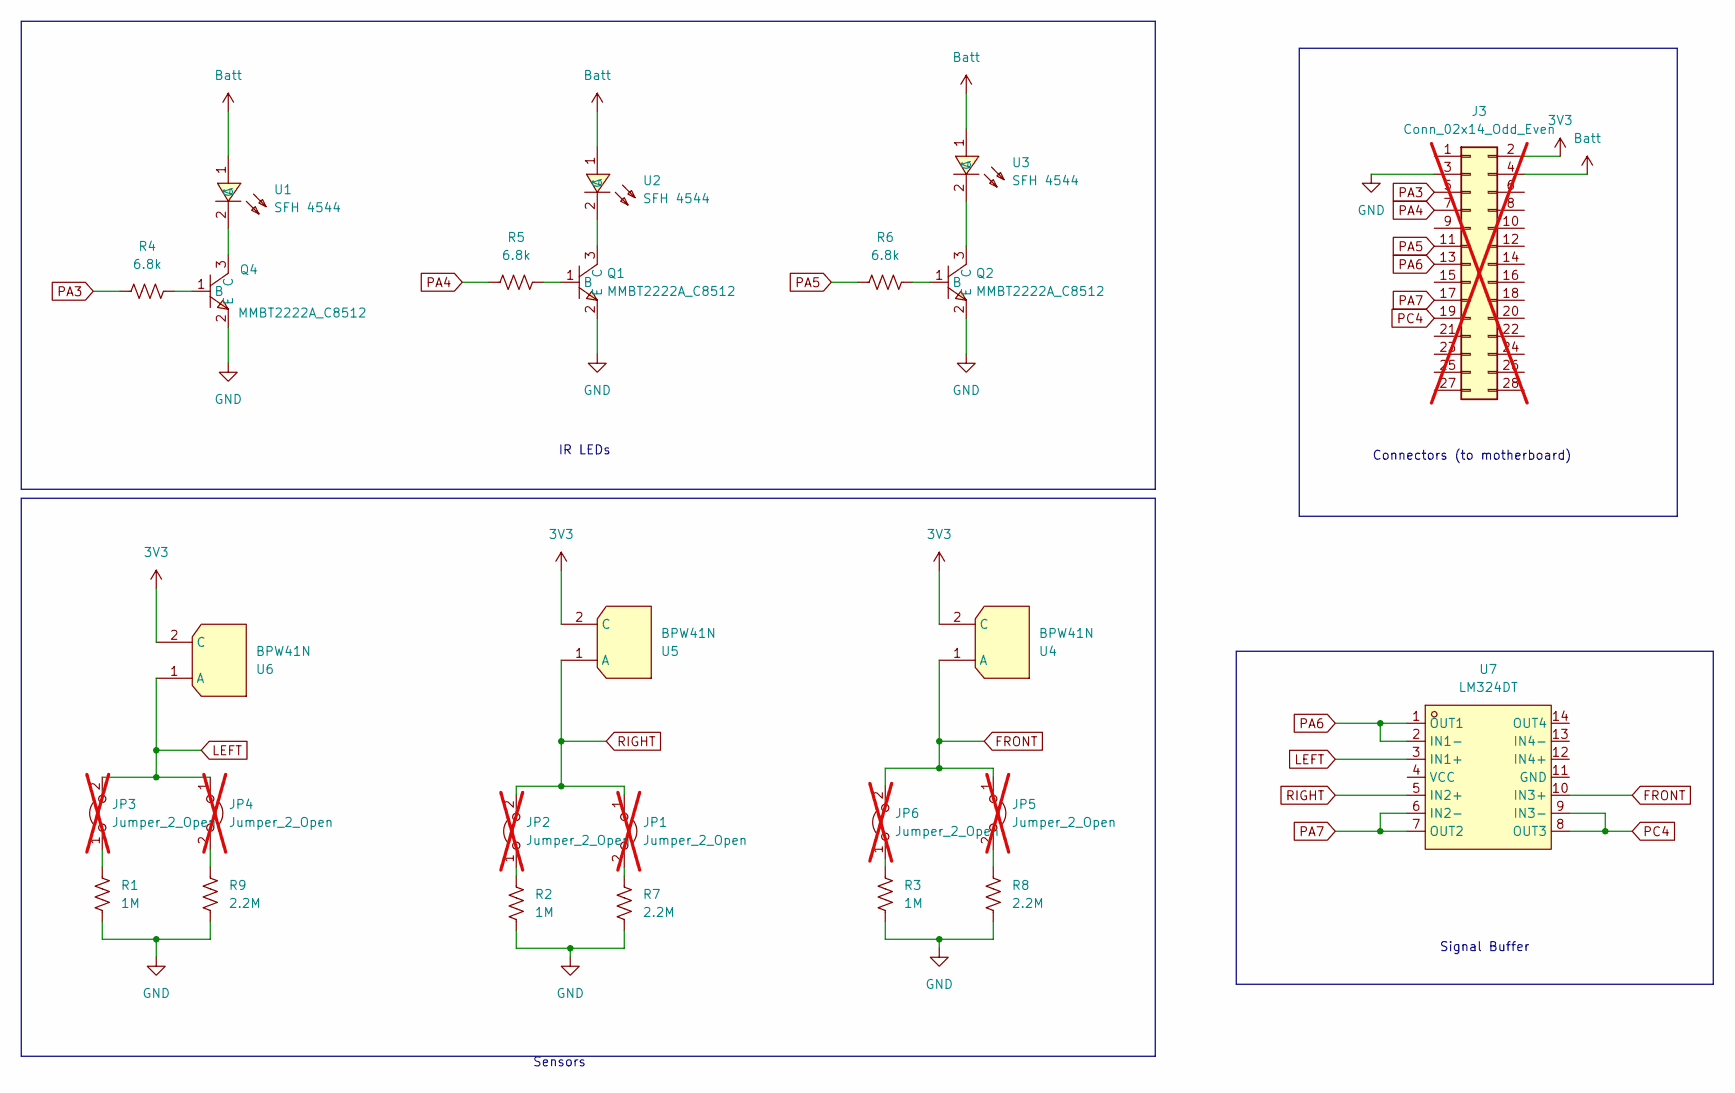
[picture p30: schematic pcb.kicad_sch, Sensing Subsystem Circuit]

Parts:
J3: Conn_02x14_Odd_Even; PinHeader_2x14_P2.54mm_Vertical; not fitted
JP1, JP2, JP3, JP4, JP5, JP6: Jumper_2_Open; SolderJumper-2_P1.3mm_Open_RoundedPad1.0x1.5mm; not fitted
Q1, Q2, Q4: MMBT2222A_C8512; SOT-23-3_L2.9-W1.3-P1.90-LS2.4-BR; LCSC Part C8512
R1, R2, R3: 1M; R_0805_2012Metric
R4, R5, R6: 6.8k; R_0805_2012Metric
R7, R8, R9: 2.2M; R_0805_2012Metric
U1, U2, U3: SFH 4544; LED_D5.0mm_Horizontal_O6.35mm_Z15.0mm; LCSC Part C2900370
U4, U5, U6: BPW41N; SENSOR-TH_BPW41N; LCSC Part C142586
U7: LM324DT; SOIC-14_L8.7-W3.9-P1.27-LS6.0-BL; LCSC Part C71035

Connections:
3V3: J3.2, U4.2 (C), U5.2 (C), U6.2 (C)
Batt: J3.4, U1.1 (A), U2.1 (A), U3.1 (A)
FRONT: JP5.1 (A), JP6.2 (B), U4.1 (A), U7.10 (IN3+)
GND: J3.3, Q1.2 (E), Q2.2 (E), Q4.2 (E), R1.2, R2.2, R3.2, R7.2, R8.2, R9.2
LEFT: JP3.2 (B), JP4.1 (A), U6.1 (A), U7.3 (IN1+)
unnamed: JP1.2 (B), R7.1
unnamed: JP2.1 (A), R2.1
unnamed: JP3.1 (A), R1.1
unnamed: JP4.2 (B), R9.1
unnamed: JP5.2 (B), R8.1
unnamed: JP6.1 (A), R3.1
unnamed: Q1.1 (B), R5.2
unnamed: Q1.3 (C), U2.2 (C)
unnamed: Q2.1 (B), R6.2
unnamed: Q2.3 (C), U3.2 (C)
unnamed: Q4.1 (B), R4.2
unnamed: Q4.3 (C), U1.2 (C)
PA3: J3.5, R4.1
PA4: J3.7, R5.1
PA5: J3.11, R6.1
PA6: J3.13, U7.1 (OUT1), U7.2 (IN1-)
PA7: J3.17, U7.6 (IN2-), U7.7 (OUT2)
PC4: J3.19, U7.8 (OUT3), U7.9 (IN3-)
RIGHT: JP1.1 (A), JP2.2 (B), U5.1 (A), U7.5 (IN2+)

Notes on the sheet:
Signal Buffer
Connectors (to motherboard)
Sensors
IR LEDs

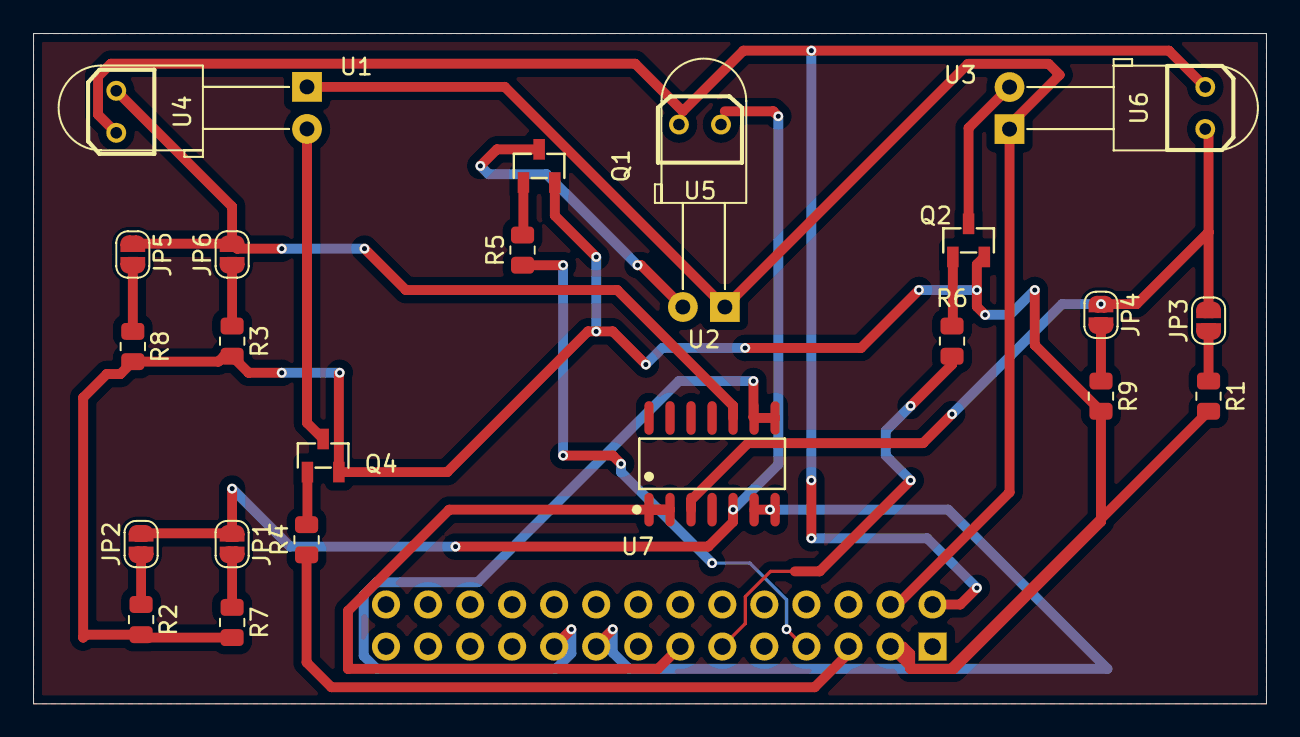
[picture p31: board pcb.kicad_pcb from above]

Board: 2 copper layers, 74.5 x 40.5 mm, 26 parts (1 on the bottom side), 24 nets.

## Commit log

2024-03-13 Created blank sensor schematics
    [sensor.kicad_pcb, sensor.kicad_sch]
2024-03-24 Project Files added
    [ProjectFiles.kicad_pcb, ProjectFiles.kicad_sch]
2024-04-21 Delete sensor directory
    To upload new schematics
    [sensor.kicad_pcb, sensor.kicad_sch]
2024-04-21 Added final design for sensing subsystem
    [BOM-pcb.csv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]
2024-04-21 Uploaded most recent kicad files and design images
    [ProjectFiles.kicad_pcb, ProjectFiles.kicad_sch]
2024-04-21 Backup Files uploaded
    [BOM-ProjectFiles.csv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]
2024-04-21 Uploaded files to correct location
    [BOM-ProjectFiles.csv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]
